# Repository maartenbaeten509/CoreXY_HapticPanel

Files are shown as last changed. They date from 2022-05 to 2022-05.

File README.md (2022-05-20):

# CoreXY_HapticPanel
[poster_BP_EA-ICT_Baeten.pdf](https://github.com/maartenbaeten509/CoreXY_HapticPanel/files/8714601/poster_BP_EA-ICT_Baeten.pdf)

# CoreXY HapticPanel: An Open System to Render Haptic Interfaces in Virtual Reality for Manufacturing Industry
The HapticPanel is a system that allows the user can interact with a product in a virtual environment simulated by different types of physical input elements e.g. buttons and sliders. The HapticPanel will position the input elements according to the user's interaction. For the haptic panel to be user friendly, the system must be sufficiently responsive. This paper looks at the option to use CoreXY as an implementation to improve system speed and characteristics. This paper also takes a closer look at different communication protocols for parsing the inputs from the input panel to the Unity framework.

## Paper information
* Link to the paper with the new CoreXY HapticPanel: https://dl.acm.org/doi/10.1145/3489849.3489901
* Link to the paper with the former Cartesian HapticPanel: https://dl.acm.org/doi/10.1145/3489849.3489901

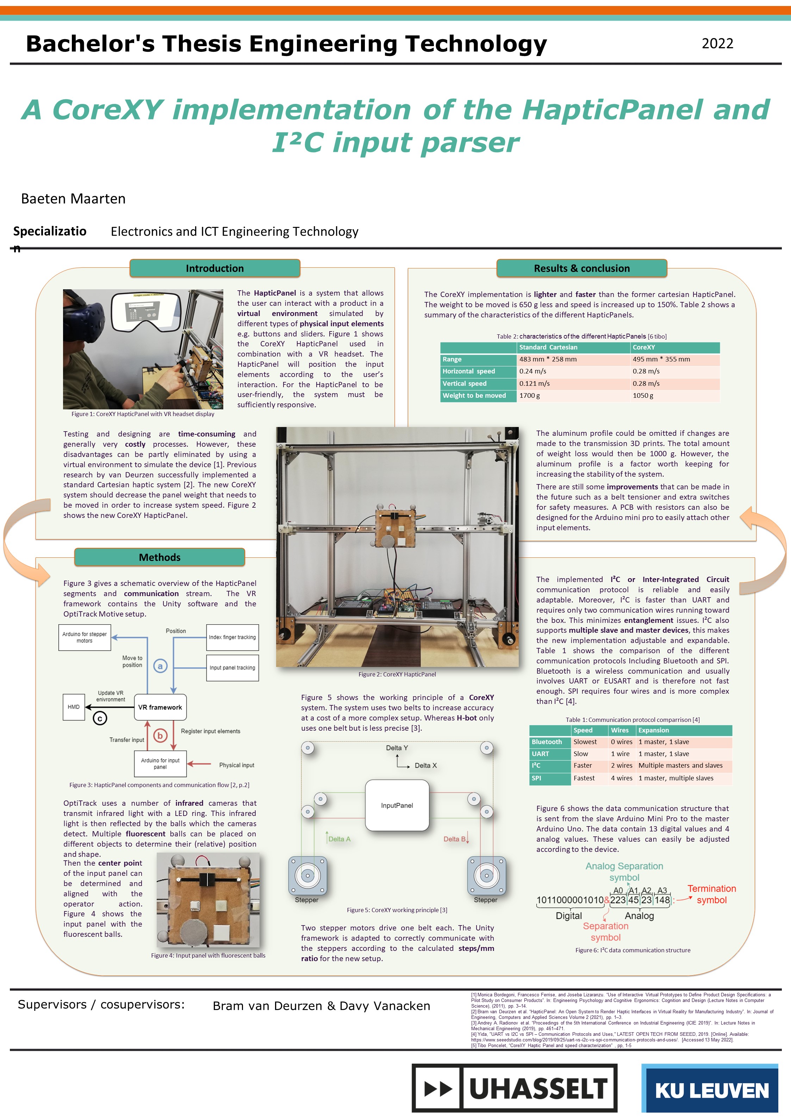
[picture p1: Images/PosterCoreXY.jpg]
HapticPanel Poster


## Quick overview
* The files can be found in the 'Platform files' directory.
* The assembly steps can be found in the wiki of this repository.
* The VR framework software can be found in the 'VR Unity core' directory.
* The Arduino software and serial parser code can be found in the 'UnityHardwareBridge' directory.

## CoreXY HapticPanel Haptic Platform
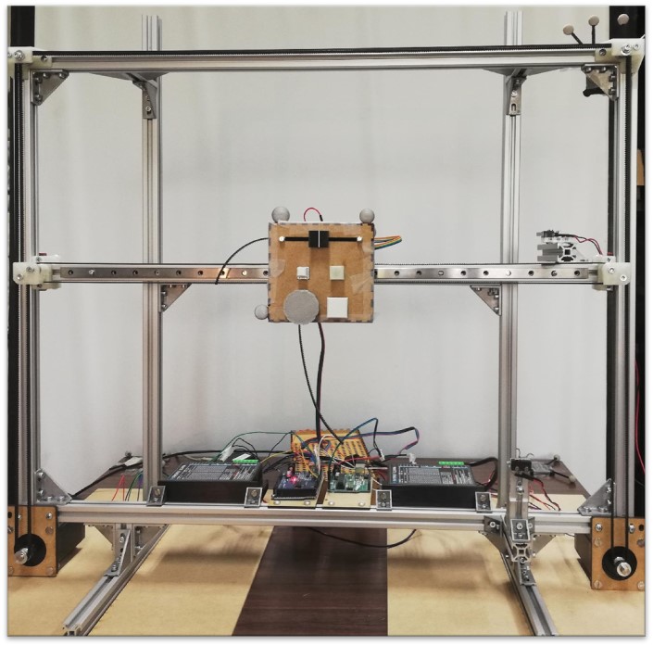
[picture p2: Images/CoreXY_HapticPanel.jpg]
HapticPanel Platform

Picture showing the Simulated Reality Haptic Platform for which the build file and instructions are shared in this repository.

## Installation instruction
1. Include SteamVR from the Unity asset store.
2. Include the OptiTrack Unity plugin, found here: https://optitrack.com/support/downloads/plugins.html
3. Deploy the Arduino software on the Arduino's controlling the stepper motors and the Arduino handling the physical input.
4. Deploy the Arduino slave code to the arduino at the input panel.
5. Open the Sample demo scene in the Demos subdirectory.
6. Align the SteamVR and OptiTrack tracking.
7. Assign the correct OptiTrack id's to the finger tracker and the input panel tracker.
8. Assign the correct COM ports.
9. Update the 'sample interface.json' to match:
	1. The Arduino port used for each physical input element
	2. The physical position of the input element on the input panel. The centre of the input panel is 0,0.

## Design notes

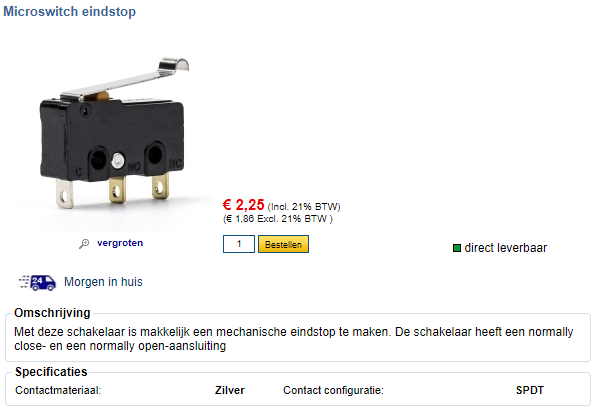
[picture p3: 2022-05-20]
TechnicalSpecifications/Switch.png

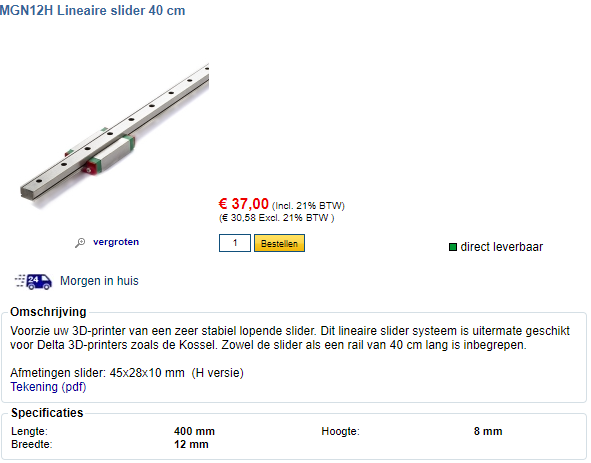
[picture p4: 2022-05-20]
TechnicalSpecifications/MGN40cm.png

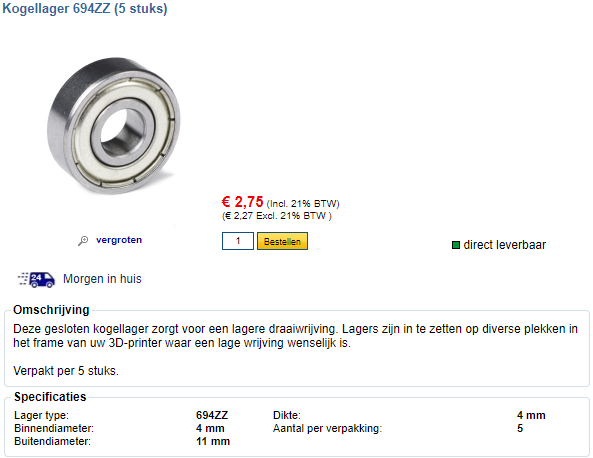
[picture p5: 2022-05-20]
TechnicalSpecifications/Bearring.png

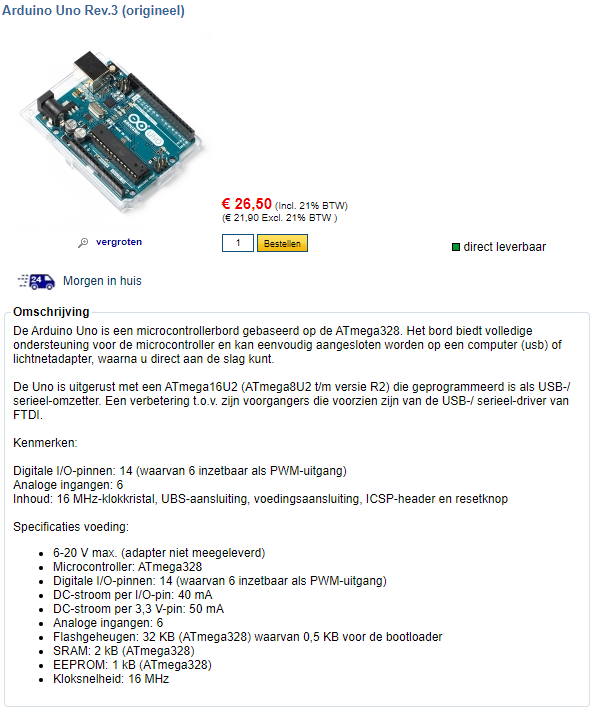
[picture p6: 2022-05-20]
TechnicalSpecifications/ArduinoUno.png

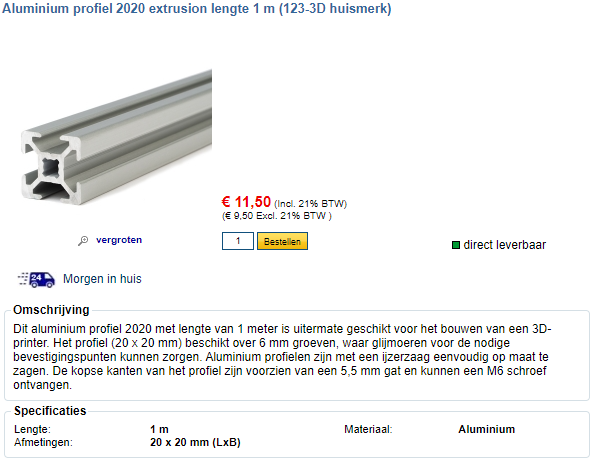
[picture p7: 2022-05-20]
TechnicalSpecifications/AluminumProfile.png

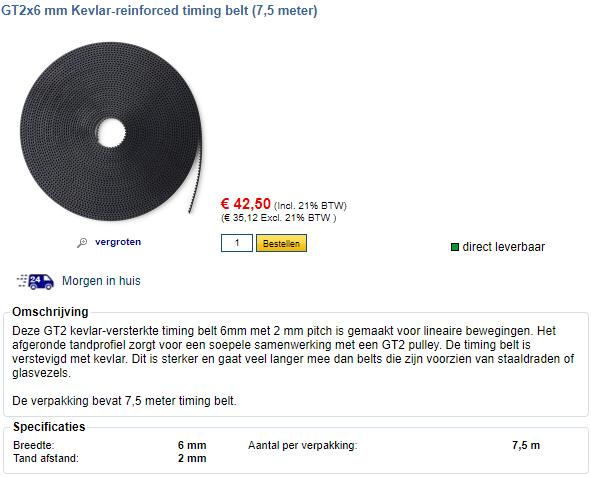
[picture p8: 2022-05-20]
TechnicalSpecifications/GT2Belt.png

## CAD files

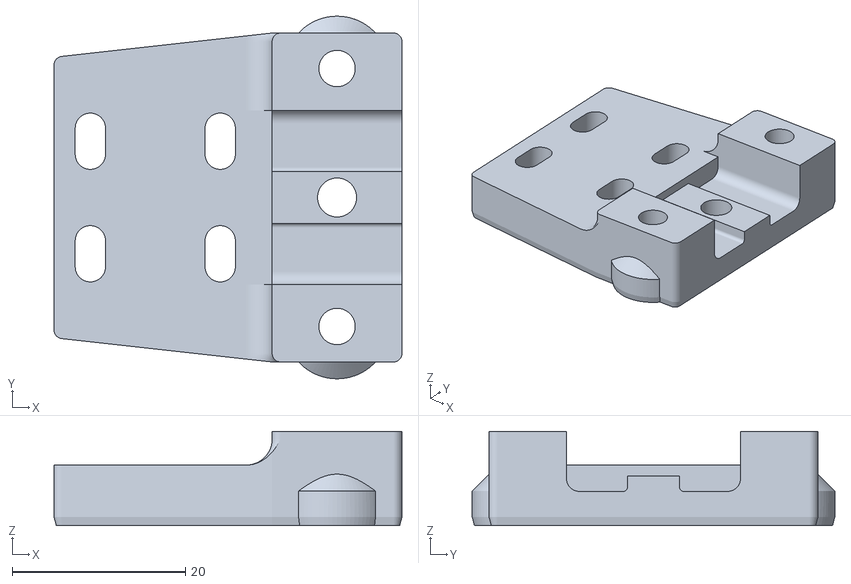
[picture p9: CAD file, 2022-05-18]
PlatformFiles/3D-prints/v2_X_bot_plate_MGN9_LR.STL
40.2 x 41.9 x 10.9

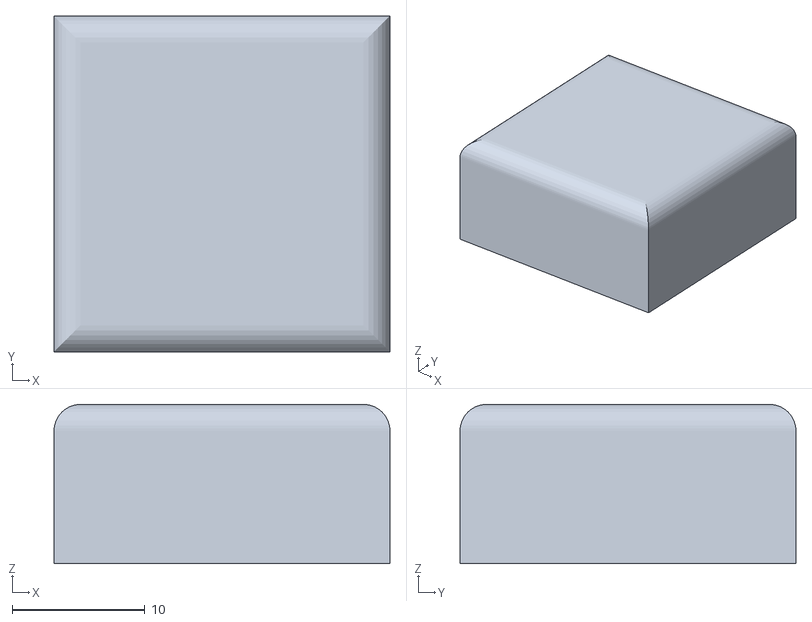
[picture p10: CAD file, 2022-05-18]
VR_Unity_Core/Assets/Demos/Sample_Demo/3d_components/Button_25x25.obj
25.3 x 25.3 x 12.0

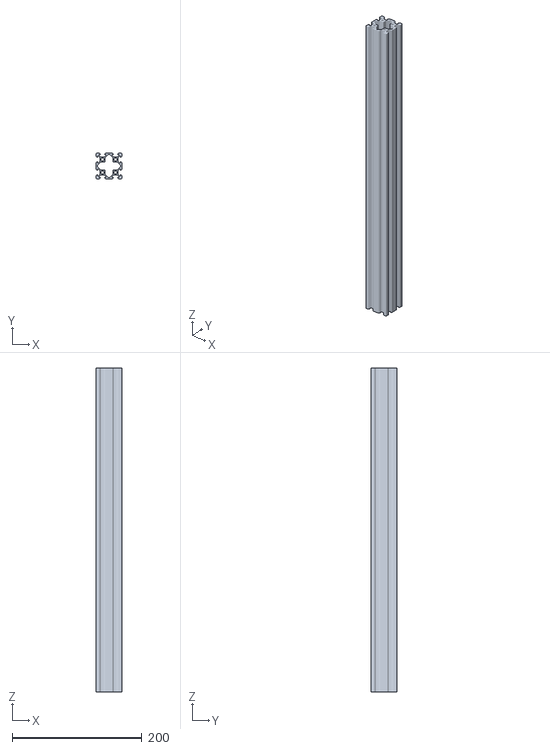
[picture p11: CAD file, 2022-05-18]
VR_Unity_Core/Assets/Demos/Sample_Demo/PickandPlace/V-slot bar double.obj
40.0 x 40.0 x 500.0

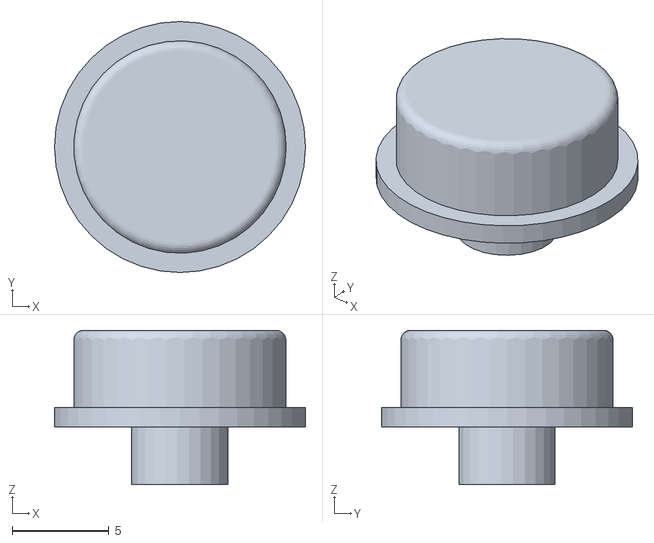
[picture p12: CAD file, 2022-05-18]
VR_Unity_Core/Assets/Interface_3D_models/Buttons/Push Button Default.obj
13.0 x 13.0 x 8.00

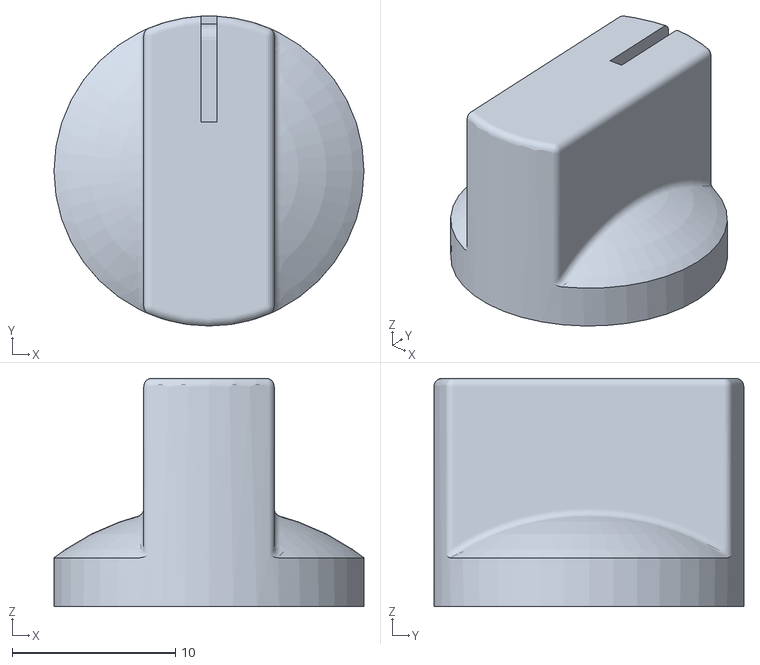
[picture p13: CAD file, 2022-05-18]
VR_Unity_Core/Assets/Interface_3D_models/Rotation/Rotation Knob Mixer.obj
19.0 x 19.0 x 14.0

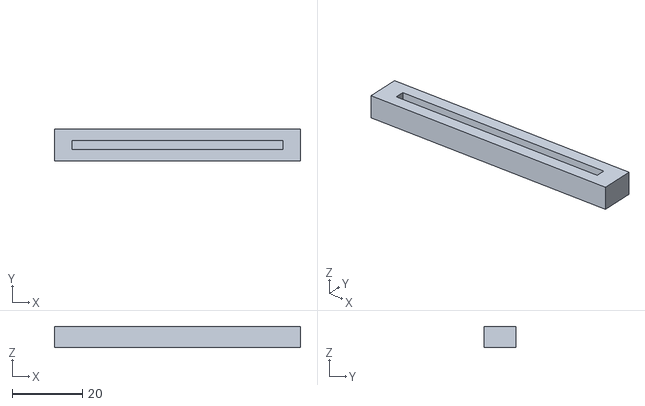
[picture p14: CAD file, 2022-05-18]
VR_Unity_Core/Assets/Interface_3D_models/Slider/Slider Small Housing scaled.obj
70.0 x 9.00 x 6.00

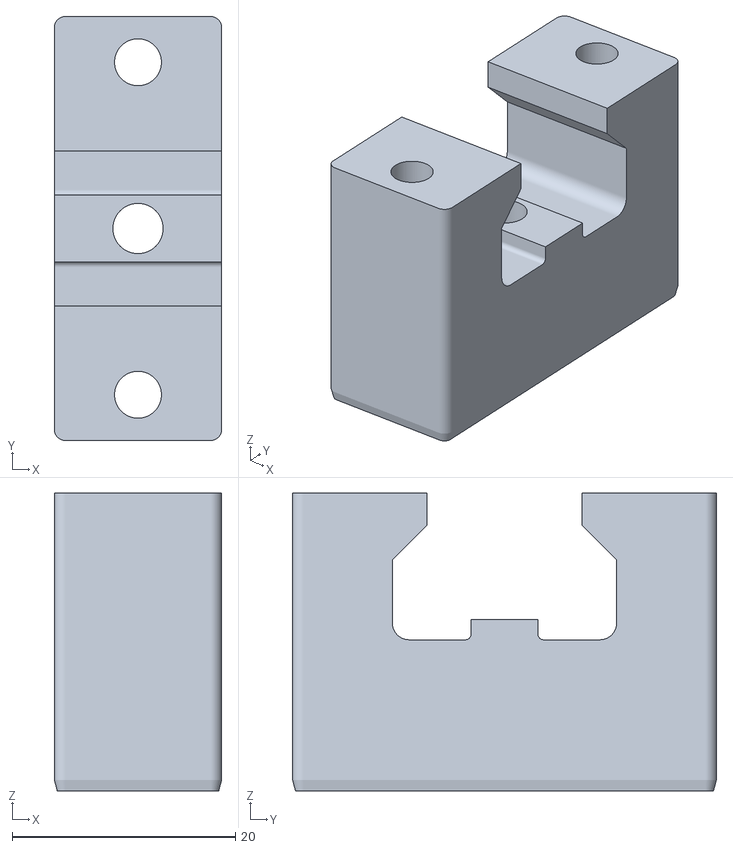
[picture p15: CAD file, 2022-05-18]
PlatformFiles/3D-prints/v2_bot_plate_1.STL
15.0 x 38.0 x 26.7

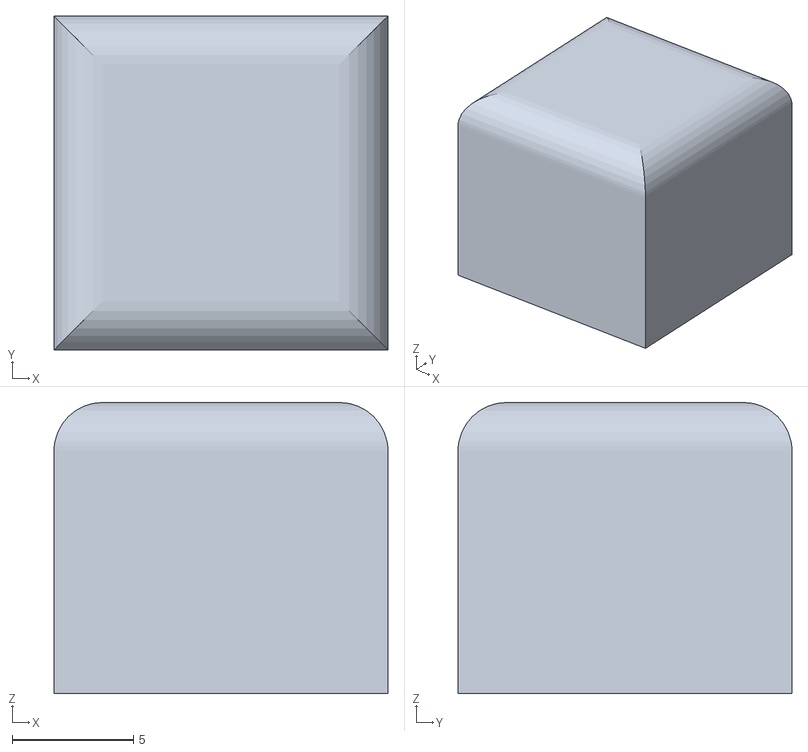
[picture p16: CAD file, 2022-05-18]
VR_Unity_Core/Assets/Demos/Sample_Demo/3d_components/Button_13x13.obj
13.8 x 13.8 x 12.0

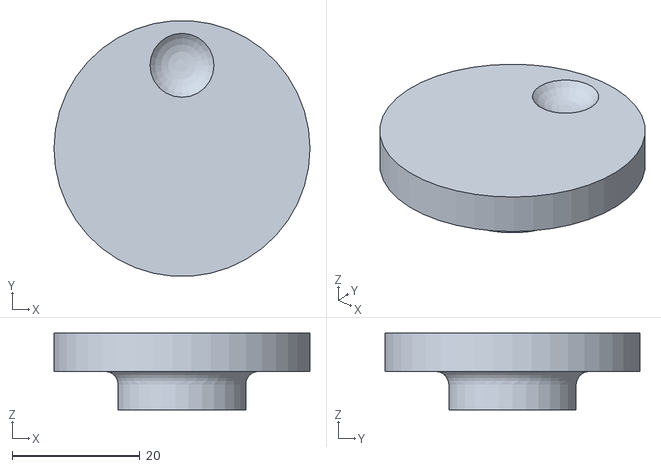
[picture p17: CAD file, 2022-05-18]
VR_Unity_Core/Assets/Interface_3D_models/Rotation/Rotation Knob Dent.obj
40.0 x 39.9 x 12.0

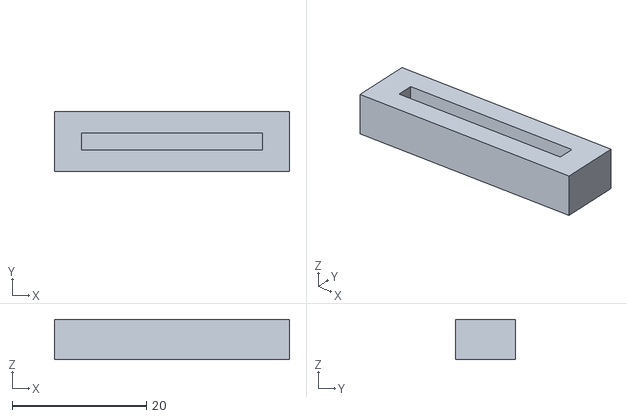
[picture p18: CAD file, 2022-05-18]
VR_Unity_Core/Assets/Interface_3D_models/Slider/Slider Small Housing.obj
35.0 x 9.00 x 6.00

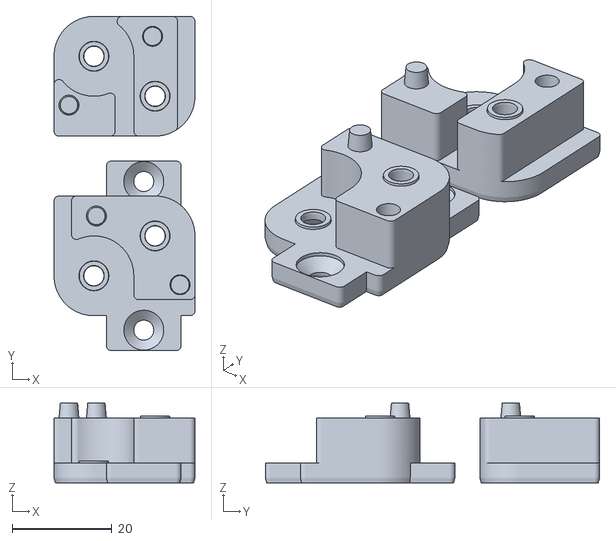
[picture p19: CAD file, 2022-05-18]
PlatformFiles/3D-prints/v2_x_idle_pulley_mount_R.STL
28.3 x 67.0 x 16.0

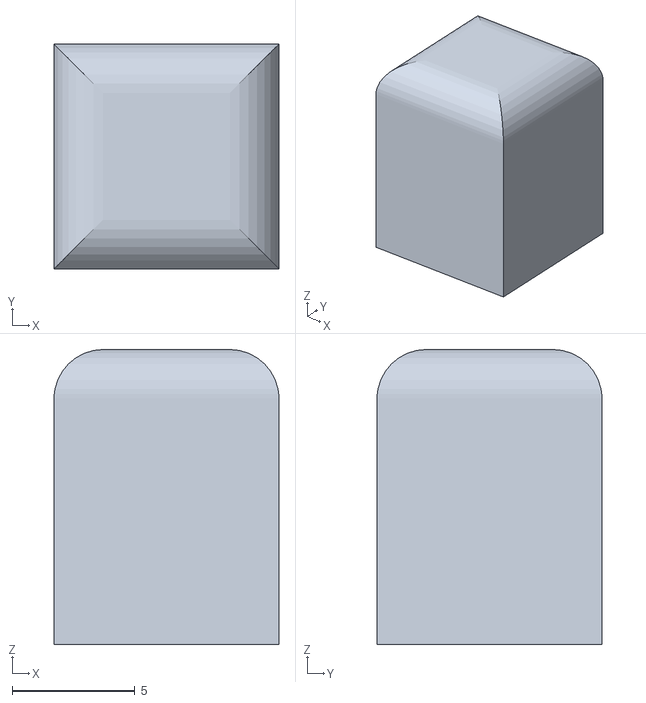
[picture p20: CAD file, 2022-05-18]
VR_Unity_Core/Assets/Demos/Sample_Demo/3d_components/Button_9x9.obj
9.15 x 9.15 x 12.0

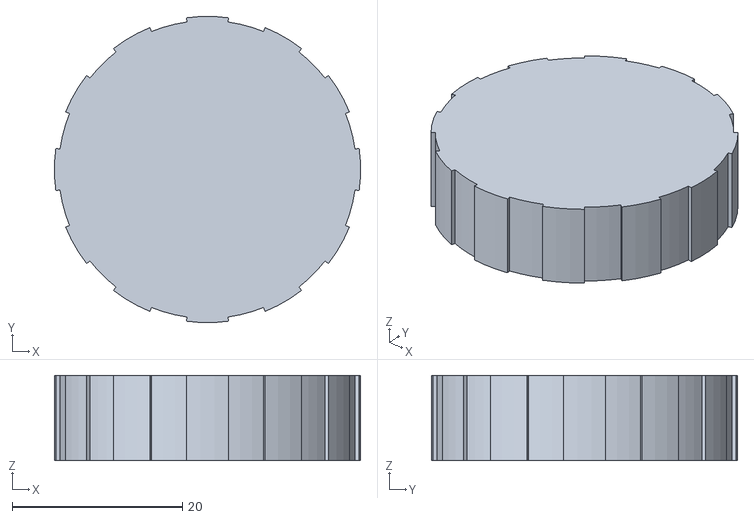
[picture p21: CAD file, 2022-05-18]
VR_Unity_Core/Assets/Interface_3D_models/Rotation/Symmetric turn knob.obj
36.0 x 36.0 x 10.0

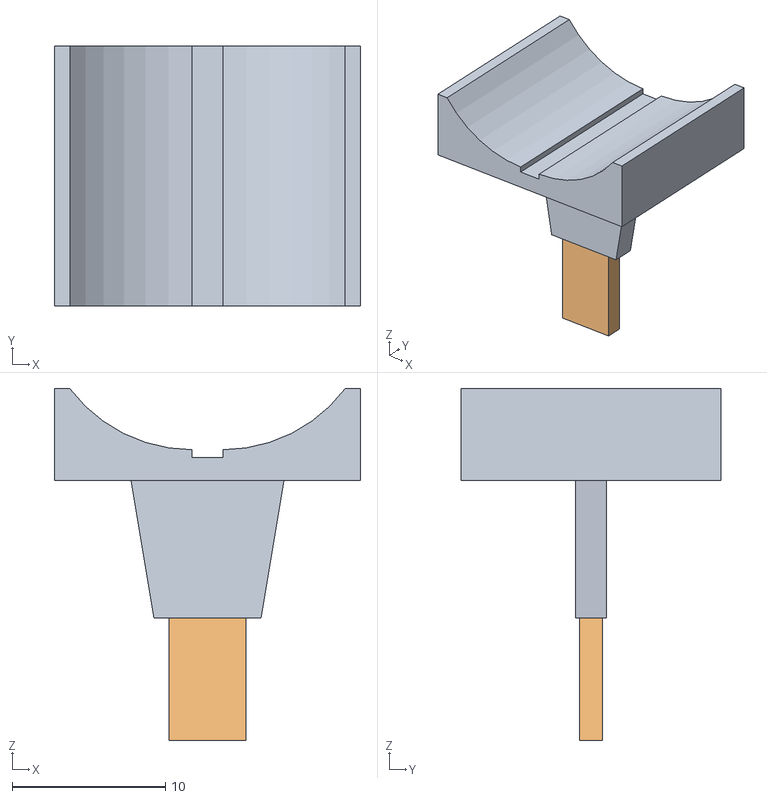
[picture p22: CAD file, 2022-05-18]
VR_Unity_Core/Assets/Interface_3D_models/Slider/Slider Finger Holder.obj
20.0 x 17.0 x 23.0

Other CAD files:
PlatformFiles/3D-prints/MGN_Platev2.stl
VR_Unity_Core/Assets/Demos/Sample_Demo/3d_components/Button_round_16.obj
VR_Unity_Core/Assets/Interface_3D_models/Rotation/Button Rectangle.obj
VR_Unity_Core/Assets/Interface_3D_models/Slider/Slider Large Housing.obj
PlatformFiles/3D-prints/Assembly1.iam
PlatformFiles/3D-prints/PanelHolderv3.stl
PlatformFiles/3D-prints/v2_MGN9_bot_plate.STL
PlatformFiles/3D-prints/v2_X_bot_plate_LR.STL
PlatformFiles/3D-prints/v2_belt_clamp_RL.STL
PlatformFiles/3D-prints/v2_x_idle_pulley_mount_L.STL
PlatformFiles/3D-prints/v2_y_idle_pulley_mount_L.STL
PlatformFiles/3D-prints/v2_y_idle_pulley_mount_R.STL

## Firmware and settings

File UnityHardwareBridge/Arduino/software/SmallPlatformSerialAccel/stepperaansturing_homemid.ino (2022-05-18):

#include <AccelStepper.h>

/*
 * Variables -----------------------------------------------------------------------------------
 */

int XLeftStop = 9; // old:  = 5
int XRightStop = 10; // old: = 4
int YTopStop = 11;
int YBottomStop = 12;

int XPUL = 7; //define Pulse pin
int XDIR = 6; //define Direction pin
int XENA = 8; //define Enable Pin

int YPUL = 4; //define Pulse pin
int YDIR = 3; //define Direction pin
int YENA = 5; //define Enable Pin

int XL = 1, XR = 1, YT = 1, YB = 1;

AccelStepper stepperX(AccelStepper::DRIVER, XPUL, XDIR);
AccelStepper stepperY(AccelStepper::DRIVER, YPUL, YDIR);


bool errorstate = false; //errorstate means no more movement allowed
const byte numChars = 32;
char receivedChars[numChars];
char tempChars[numChars];        // temporary array for use when parsing

boolean newData = false;

const bool moveWithAcceleration = false;

const float stepperXSpeed = 800;//600.0; //2000.0; //1500.0
// 800 works, 1000 doesn't, 900 doesn't
const float stepperYSpeed = 800;//600.0; // original 800.0; //1200.0; //1500.0


/* ------ stepper Y : 4 microsteps --> 800 full rotation------ */
const int STEPPER_Y_BOTTOM_LIMIT = 0; // 100
const int STEPPER_Y_UPPER_LIMIT = 1700; // 9100

///* ------ stepper X : 1 microsteps --> 200 full rotation------ */
//const int STEPPER_X_BOTTOM_LIMIT = 0; // 200
//const int STEPPER_X_UPPER_LIMIT = 500; // 8800
/* ------ stepper X : 2 microsteps --> 400 full rotation------ */
const int STEPPER_X_BOTTOM_LIMIT = 0; // 200
const int STEPPER_X_UPPER_LIMIT = 1300; // 8800

//const float stepperXAcceleration = 375.0; // 200
const float stepperXAcceleration = 1000.0; // 400 steps
const float stepperYAcceleration = 1000.0;//1500.0; 

float lastSavedPositionX = 0;
float lastSavedPositionY = 0;

/*
 * Extra functions -----------------------------------------------------------------------------------
 */

/* Stepper startup functions */


void home_x() {
  long initial_homing_a = 1;
  long initial_homing_b = 1;
  stepperY.setMaxSpeed(400);
  stepperY.setAcceleration(102.0); 
  stepperX.setMaxSpeed(400);  
  stepperX.setAcceleration(102.0); // 102
  while (digitalRead(XRightStop)) {
    stepperX.moveTo(initial_homing_a);
    stepperY.moveTo(initial_homing_b);
    initial_homing_a++;
    initial_homing_b++;
    stepperX.run();
    stepperY.run();
   
  }
  stepperX.setCurrentPosition(0);
    stepperY.setCurrentPosition(0);
  
  stepperX.setMaxSpeed(400);
    stepperY.setMaxSpeed(400);
  initial_homing_a = -1;
  initial_homing_b = -1;
  delay(200);
  while (!digitalRead(XRightStop)) {
    stepperX.moveTo(initial_homing_a);
     stepperY.moveTo(initial_homing_b);    
    initial_homing_a--;
    initial_homing_b--;
    stepperX.run();
    stepperY.run();
    
    
  }
    
  stepperY.setCurrentPosition(0);
  stepperX.setCurrentPosition(0);
 
}

void home_y() {
  long initial_homing_a = 1;
  long initial_homing_b = -1;
  
  stepperX.setMaxSpeed(400);  
  stepperX.setAcceleration(102.0); // 102
  stepperY.setMaxSpeed(400);
  stepperY.setAcceleration(102.0); 

  while (digitalRead(YBottomStop)) {
    stepperX.moveTo(initial_homing_a);
    stepperY.moveTo(initial_homing_b);
    initial_homing_a++;
    initial_homing_b--;
    stepperX.run();
    stepperY.run();
  }
  stepperY.setCurrentPosition(0);
  
  stepperX.setCurrentPosition(0);
  stepperY.setMaxSpeed(400);
  stepperX.setMaxSpeed(400);
  initial_homing_a = -1;
  initial_homing_b = 1;
  delay(200);
  while (!digitalRead(YBottomStop)) {
    stepperY.moveTo(initial_homing_b);
    stepperX.moveTo(initial_homing_a);
    initial_homing_b++;
    initial_homing_a--;
    stepperX.run();
    stepperY.run();

  }

  stepperY.setCurrentPosition(0);
  stepperX.setCurrentPosition(0);
}


void MoveSteppersAccel(long goToPositionX, long goToPositionY){
  long diffX;
  long diffY;
  // X AXIS
    if (goToPositionX >= STEPPER_X_BOTTOM_LIMIT && goToPositionX <= STEPPER_X_UPPER_LIMIT) 
    {
      diffX = lastSavedPositionX - goToPositionX;  
      lastSavedPositionX = goToPositionX;
     // stepperX.moveTo(goToPositionX);
    }
    // outside range, move to last saved position
    else
    {
      //stepperX.moveTo(lastSavedPositionX);
      diffX = 0;
    }
    // Y AXIS
    if (goToPositionY >= STEPPER_Y_BOTTOM_LIMIT && goToPositionY <= STEPPER_Y_UPPER_LIMIT) 
    {
      diffY = lastSavedPositionY - goToPositionY;
      lastSavedPositionY = goToPositionY;
     // stepperY.moveTo(goToPositionY);
    }
    // outside range, move to last saved position
    else
    {
      //stepperY.moveTo(lastSavedPositionY);
      diffY = 0;
      
    }
}




void MoveSteppersConstant(long goToPositionX, long goToPositionY){
  long diffX =0;
  long diffY =0;
  // X AXIS
    if (goToPositionY >= STEPPER_Y_BOTTOM_LIMIT && goToPositionY <= STEPPER_Y_UPPER_LIMIT && goToPositionX >= STEPPER_X_BOTTOM_LIMIT && goToPositionX <= STEPPER_X_UPPER_LIMIT) 
    {
     // diffX =   goToPositionX - lastSavedPositionX ;
      lastSavedPositionX = goToPositionX;
      stepperX.moveTo(-goToPositionX - goToPositionY);
      // Move with constant speed
      stepperX.setSpeed(stepperXSpeed);
    }
    // outside range, move to last saved position
    else
    {
      stepperX.moveTo(-lastSavedPositionX - lastSavedPositionY);
     
      // Move with constant speed
      stepperX.setSpeed(stepperXSpeed);
    }
    // Y AXIS
    if (goToPositionY >= STEPPER_Y_BOTTOM_LIMIT && goToPositionY <= STEPPER_Y_UPPER_LIMIT && goToPositionX >= STEPPER_X_BOTTOM_LIMIT && goToPositionX <= STEPPER_X_UPPER_LIMIT) 
    {
     // diffY = goToPositionY - lastSavedPositionY ;
      lastSavedPositionY = goToPositionY;
      stepperY.moveTo(goToPositionX - goToPositionY);
      // Move with constant speed
      stepperY.setSpeed(stepperYSpeed);
    }
    // outside range, move to last saved position
    else
    {
      stepperY.moveTo(lastSavedPositionX - lastSavedPositionY);
     // diffY = 0;
      // Move with constant speed
      stepperY.setSpeed(stepperYSpeed);
    }
    //MovePanel(diffX,diffY);
  //long moveA = diffX + diffY;
  //long moveB = diffX - diffY;
  //stepperY.setSpeed(stepperYSpeed);
  //stepperX.setSpeed(stepperXSpeed);
  //stepperX.moveTo(moveA);
  //stepperY.moveTo(moveB);
  //Serial.println(lastSavedPositionY);
  //Serial.println(lastSavedPositionX);
    
}


/* Serial communication */

void SerialCommandListener() {
  recvWithStartEndMarkers();
  if (newData == true) {
    strcpy(tempChars, receivedChars);
    char * strtokIndx; // this is used by strtok() as an index
    long positionX = 0;
    long positionY = 0;

    strtokIndx = strtok(tempChars, ",");     // get the first part
    positionX = atol(strtokIndx); // Convert to travelX

    strtokIndx = strtok(NULL, ","); // this continues where the previous call left off
    positionY = atol(strtokIndx);     // Convert to travelY

    strtokIndx = strtok(NULL, ","); // this continues where the previous call left off
    if(strtokIndx != NULL){
      if(*strtokIndx == 'P'){
        // Set the new position of the platform.
        stepperX.setCurrentPosition(positionX);
        stepperX.setMaxSpeed(stepperXSpeed);
        stepperY.setCurrentPosition(positionY);
        stepperY.setMaxSpeed(stepperYSpeed);
      }
      else {
        Serial.print("Wrong command, should be P: ");
      }
    }
    else {
      if(moveWithAcceleration)
        MoveSteppersAccel(positionX, positionY);
      else
        MoveSteppersConstant(positionX, positionY);
    }


    /* ------ Steppers Control ------- */

    

    newData = false;
  }

  if (!errorstate) {
    if(moveWithAcceleration)
    {
      // Move with acceleration
      stepperX.run();
      stepperY.run();
    }
    else {
      // Move with constant speed
      stepperX.runSpeedToPosition();
      stepperY.runSpeedToPosition();
    }
  }
}

void recvWithStartEndMarkers() {
  static boolean recvInProgress = false;
  static byte ndx = 0;
  char startMarker = '<';
  char endMarker = '>';
  char rc;

  while (Serial.available() > 0 && newData == false) {
    rc = Serial.read();

    if (recvInProgress == true) {
      if (rc != endMarker) {
        receivedChars[ndx] = rc;
        ndx++;
        if (ndx >= numChars) {
          ndx = numChars - 1;
        }
      }
      else {
        receivedChars[ndx] = '\0'; // terminate the string
        recvInProgress = false;
        ndx = 0;
        newData = true;
      }
    }

    else if (rc == startMarker) {
      recvInProgress = true;
    }
  }
}

/* 
 *  Main setup and loop -----------------------------------------------------------------------------------
 */

void setup() {
  // put your setup code here, to run once:
  pinMode(XENA, OUTPUT);
  pinMode(YENA, OUTPUT);
  pinMode(13, OUTPUT);

  pinMode(XLeftStop, INPUT_PULLUP);
  pinMode(XRightStop, INPUT_PULLUP);
  pinMode(YTopStop, INPUT_PULLUP);
  pinMode(YBottomStop, INPUT_PULLUP);

  digitalWrite(XENA, LOW);
  digitalWrite(YENA, LOW);

  Serial.begin(9600); // 115200
  
  Serial.println("Startinig up!");
  delay(3);

  home_x();

  Serial.println("Home x finished");
  
  home_y();
  
  Serial.println("homing finished");

  //stepperX.moveTo(10);
  //stepperY.moveTo(10);


  
  stepperX.setMaxSpeed(stepperXSpeed);
  stepperX.setAcceleration(stepperXAcceleration);

  stepperY.setMaxSpeed(stepperYSpeed);
  stepperY.setAcceleration(stepperYAcceleration);
  MoveSteppersConstant(500,500);
}

void loop() {
 // Serial.print("test");
  // REad input from the stops
  XL = digitalRead(XLeftStop);
  XR = digitalRead(XRightStop);
  YT = digitalRead(YTopStop);
  YB = digitalRead(YBottomStop);

  //Serial.print("XL: ");
  //Serial.print(XL);
  //Serial.print(" XR: ");
  //Serial.print(XR);
  //Serial.print(" YT: ");
 // Serial.print(YT);
 // Serial.print(" YB: ");
 // Serial.println(YB);

  SerialCommandListener(); 

  // When a end stop is hit, home back to 0 position for that axis.
//  if (!(XL)) {
//    Serial.println("Home X Left  triggered");
//    stepperX.stop();
//    home_x();
//    stepperX.setMaxSpeed(stepperXSpeed);
//    stepperX.setAcceleration(stepperXAcceleration);
//    
//  }
//  if (!(XR)) {
//    Serial.println("Home X Right triggered");
//    stepperX.stop();
//    home_x();
//    stepperX.setMaxSpeed(stepperXSpeed);
//    stepperX.setAcceleration(stepperXAcceleration);
//    
//  }
//
//  if (!(YT)) {
//    Serial.println("Home -Y- Top triggered");
//    stepperY.stop();
//    home_y();
//    stepperY.setMaxSpeed(stepperYSpeed);
//    stepperY.setAcceleration(stepperYAcceleration);
//    
//  }
//
//  if (!(YB)) {
//    Serial.println("Home -Y- Bottom triggered");
//    stepperY.stop();
//    home_y();
//    stepperY.setMaxSpeed(stepperYSpeed);
//    stepperY.setAcceleration(stepperYAcceleration);
//    
//  }
  
}

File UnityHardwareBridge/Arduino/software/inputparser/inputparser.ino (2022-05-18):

/*
 * TODO
 * - Make reset command
 * - Create error message
 * - Fix memory limitations
 */

// Used for rotary encoder
#include "Rotary.h"
#include <Wire.h> //Added code By Maarten Baeten

const int numberOfDigitalPins = 14;
const int numberOfAnalogPins = 4;

typedef enum { UNSET = 0, MESSAGE, COMMAND, DATA, EXTENDEDDATA, ERRORMESSAGE } messagetype_t;

int command = 0;
int commanddata = -1;
int state = 0; //0 = start, 1 = wait command, 2 = wait command data, -1 error
int messagesize;
int messagesizeread;
messagetype_t messagetype;
char messagepayload[128]; // Reduced from 1024 to save some program memory
bool messagedone = false;

typedef enum { INACTIVE = 0, BUTTON, ROTARY_ENCODER, NUMBEROFDIGITALTYPES } digitaltype_t;
typedef enum analogtype_t { INACTIVE_A = 0, SLIDER, NUMBEROFANALOGTYPES };
int digitaltype[numberOfDigitalPins];
int analogtype[numberOfAnalogPins];
int analogInputPins[] = { A0, A1, A2, A3};

String analogtypeS[numberOfAnalogPins];//Added code By Maarten Baeten
int analogtypeI[numberOfAnalogPins];//Added code By Maarten Baeten
String inputs = ""; //Added code By Maarten Baeten
int k; //Added code By Maarten Baeten

Rotary* rotaryEncoderList[numberOfDigitalPins];

void writeSizedMessage(char code, const char* reply) {
  Serial.print(F("{")); // F("...") used to save some program memory
  Serial.write(code);
  Serial.write(strlen(reply));
  Serial.write(reply, strlen(reply));
  Serial.print(F("}"));
}

void setup() {
  Wire.begin();        // join i2c bus (address optional for master) X
  
  Serial.begin(9600);
  writeSizedMessage('M', "Starting device...");

  for (int i = 0; i < numberOfDigitalPins; ++i) {
    digitaltype[i] = digitaltype_t::INACTIVE;
    rotaryEncoderList[i] = nullptr;
    analogtype[i] = analogtype_t::INACTIVE_A;
  }
}

void processmessage() {
  if (messagetype == messagetype_t::COMMAND) {
    if (messagepayload[0] == 'A') { 
      if (messagepayload[2] == 'I')
        messagepayload[2] = digitaltype_t::INACTIVE;
      if (messagepayload[2] == 'B') // Button case
        messagepayload[2] = digitaltype_t::BUTTON;
//        messagepayload[1] = messagepayload[1] - '0'; // I2C change
//      Serial.print(messagepayload[1]); Serial.print(" payload < numberOFPins "); Serial.println(numberOfDigitalPins); Serial.println(3 < 14);
//      Serial.println(messagepayload[1] < numberOfDigitalPins);
//      Serial.println(messagepayload[2] < digitaltype_t::NUMBEROFDIGITALTYPES);
      if (messagepayload[1] < numberOfDigitalPins && messagepayload[2] < digitaltype_t::NUMBEROFDIGITALTYPES) {
        //pinMode(messagepayload[1], INPUT); // I2C change
        digitaltype[messagepayload[1]] = messagepayload[2];

        Serial.print(F("{M"));
        Serial.write(37);
        Serial.print(F("Command executed: "));
        Serial.write(messagepayload[0]);
        Serial.print(F(": type "));
        Serial.write(messagepayload[2] + '0');
        Serial.print(F(" on port "));
        Serial.write(messagepayload[1] + '0');
        Serial.print(F("}"));
      } else {
        //todo, error info
        Serial.println(messagepayload[1] < numberOfDigitalPins);
        Serial.println(messagepayload[2] < digitaltype_t::NUMBEROFDIGITALTYPES);
        Serial.println(messagepayload[1]);
        Serial.write(messagepayload[1]);
        Serial.println(F("Invalid port number given."));
      }
    } else if(messagepayload[0] == 'R'){ // Rotary encoder case --> 2 ports
      if (messagepayload[3] == 'I')
        messagepayload[3] = digitaltype_t::INACTIVE;
      if (messagepayload[3] == 'R')
        messagepayload[3] = digitaltype_t::ROTARY_ENCODER;
      
      if (messagepayload[1] < numberOfDigitalPins && messagepayload[2] < numberOfDigitalPins && messagepayload[3] < digitaltype_t::NUMBEROFDIGITALTYPES && messagepayload[4] < digitaltype_t::NUMBEROFDIGITALTYPES) {
        // Assume that the pin1 + 1 == pin2
        digitaltype[messagepayload[1]] = messagepayload[3];
        digitaltype[messagepayload[2]] = messagepayload[3];
        // Setup rotary encoder in the list position of port 1
        rotaryEncoderList[messagepayload[1]] = new Rotary(messagepayload[1],messagepayload[2]);

        // TODO Fix this.
        Serial.print(F("{M"));
        Serial.write(37);
        Serial.print(F("Command executed: "));
        Serial.write(messagepayload[0]);
        Serial.print(F(": type "));
        Serial.write(messagepayload[2] + '0');
        Serial.print(F(" on port "));
        Serial.write(messagepayload[1] + '0');
        Serial.print(F("}"));
      } else {
       //todo, error info
      }
    } else if (messagepayload[0] == 'S'){ // Slider case: Analog 1 port
        if (messagepayload[2] == 'I')
          messagepayload[2] = analogtype_t::INACTIVE_A;
        if (messagepayload[2] == 'S')
          messagepayload[2] = analogtype_t::SLIDER;
//           messagepayload[1] = messagepayload[1] - '0'; // I2C change
        // Process information
        if (messagepayload[1] < numberOfAnalogPins && messagepayload[2] < analogtype_t::NUMBEROFANALOGTYPES) {

          analogtype[messagepayload[1]] = messagepayload[2];
  
          Serial.print(F("{M"));
          Serial.write(3);
//          Serial.print(F("Command executed: "));
          Serial.write(messagepayload[0]);
//          Serial.print(F(": type "));
          Serial.write('A');
//          Serial.print(F(" on port "));
          Serial.write(messagepayload[1]);
          Serial.print(F("}"));
        } else {
          //todo, error info
          Serial.println(F("Invalid port number given."));
      }
    } else if (messagepayload[0] == 'I') {
      writeSizedMessage('I', "{\"devicetype\":\"inputpasser\",\"version\":2}");
    } else {
      // no message payload matched
    }
  } else if (messagetype == messagetype_t::ERRORMESSAGE) {
    Serial.print(F("{X"));
    Serial.write(7 + messagesize);
    Serial.print(F("Error: "));
    Serial.write(messagepayload, messagesize);
    Serial.print(F("}"));
  } else {
    writeSizedMessage('M', "Message received");
  }
  command = 0;
  messagesize = 0;
  messagesizeread = 0;
  messagetype = messagetype_t::UNSET;
  messagedone = false;
}

void setErrorInParsing(const char* message) {
  messagetype = messagetype_t::ERRORMESSAGE;
  strcpy(messagepayload, message);
  messagesize = strlen(message);
  messagesizeread = messagesize;
  messagedone = true;
  state = 0;
}
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
